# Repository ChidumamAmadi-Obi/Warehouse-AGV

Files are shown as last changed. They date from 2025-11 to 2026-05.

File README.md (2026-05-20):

# Warehouse AGV 
*(3rd Year Capstone Project)*

Automated Guided Vehicle that transports loads along predetermined paths. Features line following, obstacle detection, location tracking, and PS4 controller input via Bluetooth. Built with a Finite State Machine (FSM) architecture with LED/buzzer alerts for user feedback.

### Links
 - [**Demo Video**](https://github.com/user-attachments/assets/4ddb8e79-1c91-4d6d-a385-816ef9b9aa53) <br>
 - [*STL Files*](https://github.com/ChidumamAmadi-Obi/Warehouse-AGV/tree/main/mechanical%20design/STL%20FIles) <br>
 - [*Gerber Files*](https://github.com/ChidumamAmadi-Obi/Warehouse-AGV/tree/main/hardware/gerbers-files) <br>
 - [*Schematic Diagram*](https://github.com/ChidumamAmadi-Obi/Warehouse-AGV/blob/main/hardware/schematic-pdf.pdf) <br>
 - [*Firmware Source Code*](https://github.com/ChidumamAmadi-Obi/Warehouse-AGV/tree/main/firmware) <br>



### Features
- PS4 Bluetooth controller for destination waypoints
- Line following with obstacle avoidance
- Real-time location tracking with waypoint markers on track
- Finite State Machine with robust transitions 
- Visual/audio alerts (LEDs & buzzer)
- 3D printable chassis (STL files included)
- Custom PCB with integrated motor driver, voltage regulation and sensor headers

### Firmware Prerequisites
The chosen controller needs to be paired with the ESP32’s Bluetooth MAC address before use.
Additionally, project also relies on [this](https://github.com/pablomarquez76/PS4_Controller_Host/tree/main) ps4 controller library to handle the Bluetooth communication between the ESP32 and the PS4 controller.

Once this library is installed it is to be inserted into the `./lib` PlatformIO project directory

### Custom PCB


### Schematic Diagram


### State Diagram


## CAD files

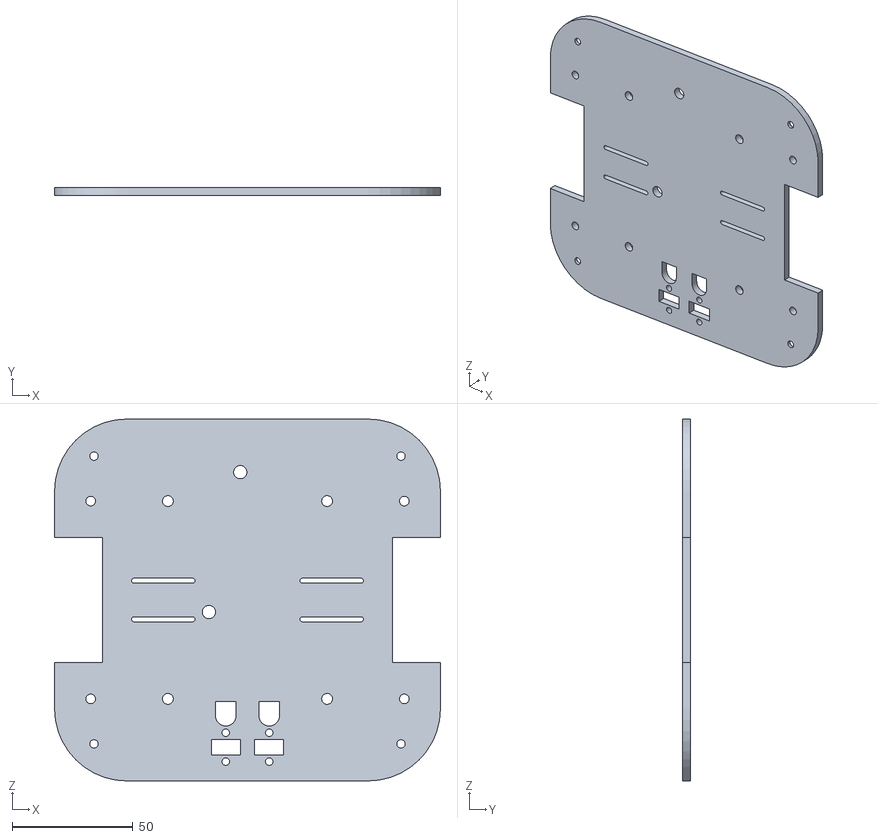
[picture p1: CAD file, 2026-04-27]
mechanical design/STL FIles/Bottom.STL
160.0 x 3.50 x 150.0

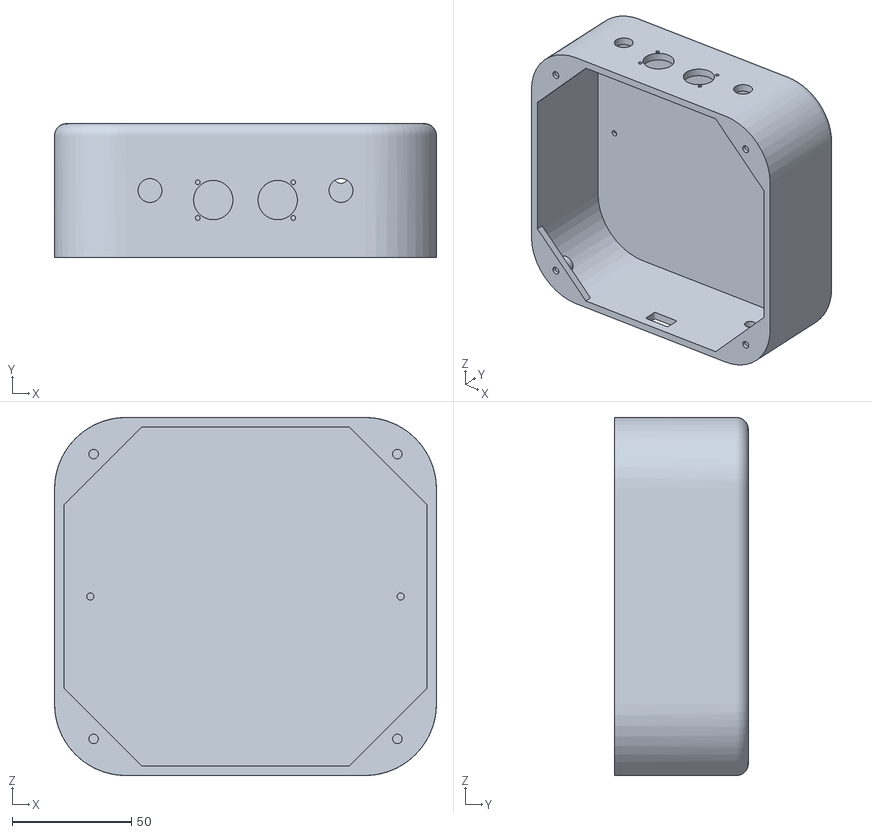
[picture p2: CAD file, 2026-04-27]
mechanical design/STL FIles/Body.STL
160.0 x 56.0 x 150.0

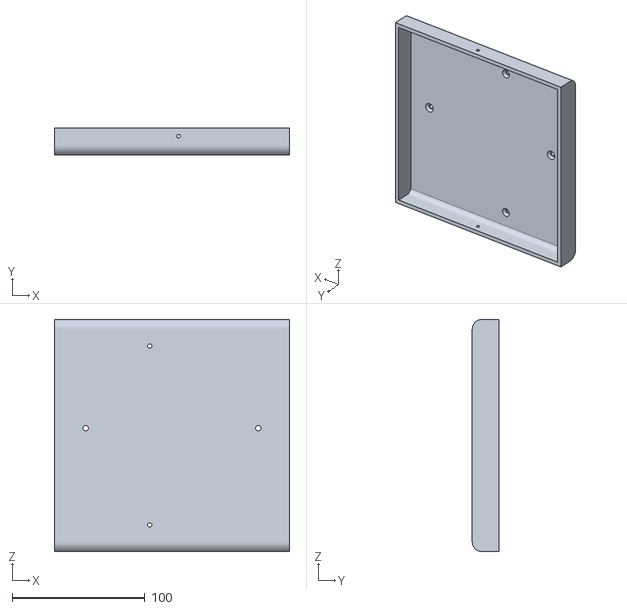
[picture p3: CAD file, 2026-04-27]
mechanical design/STL FIles/Top.STL
177.0 x 20.0 x 175.0

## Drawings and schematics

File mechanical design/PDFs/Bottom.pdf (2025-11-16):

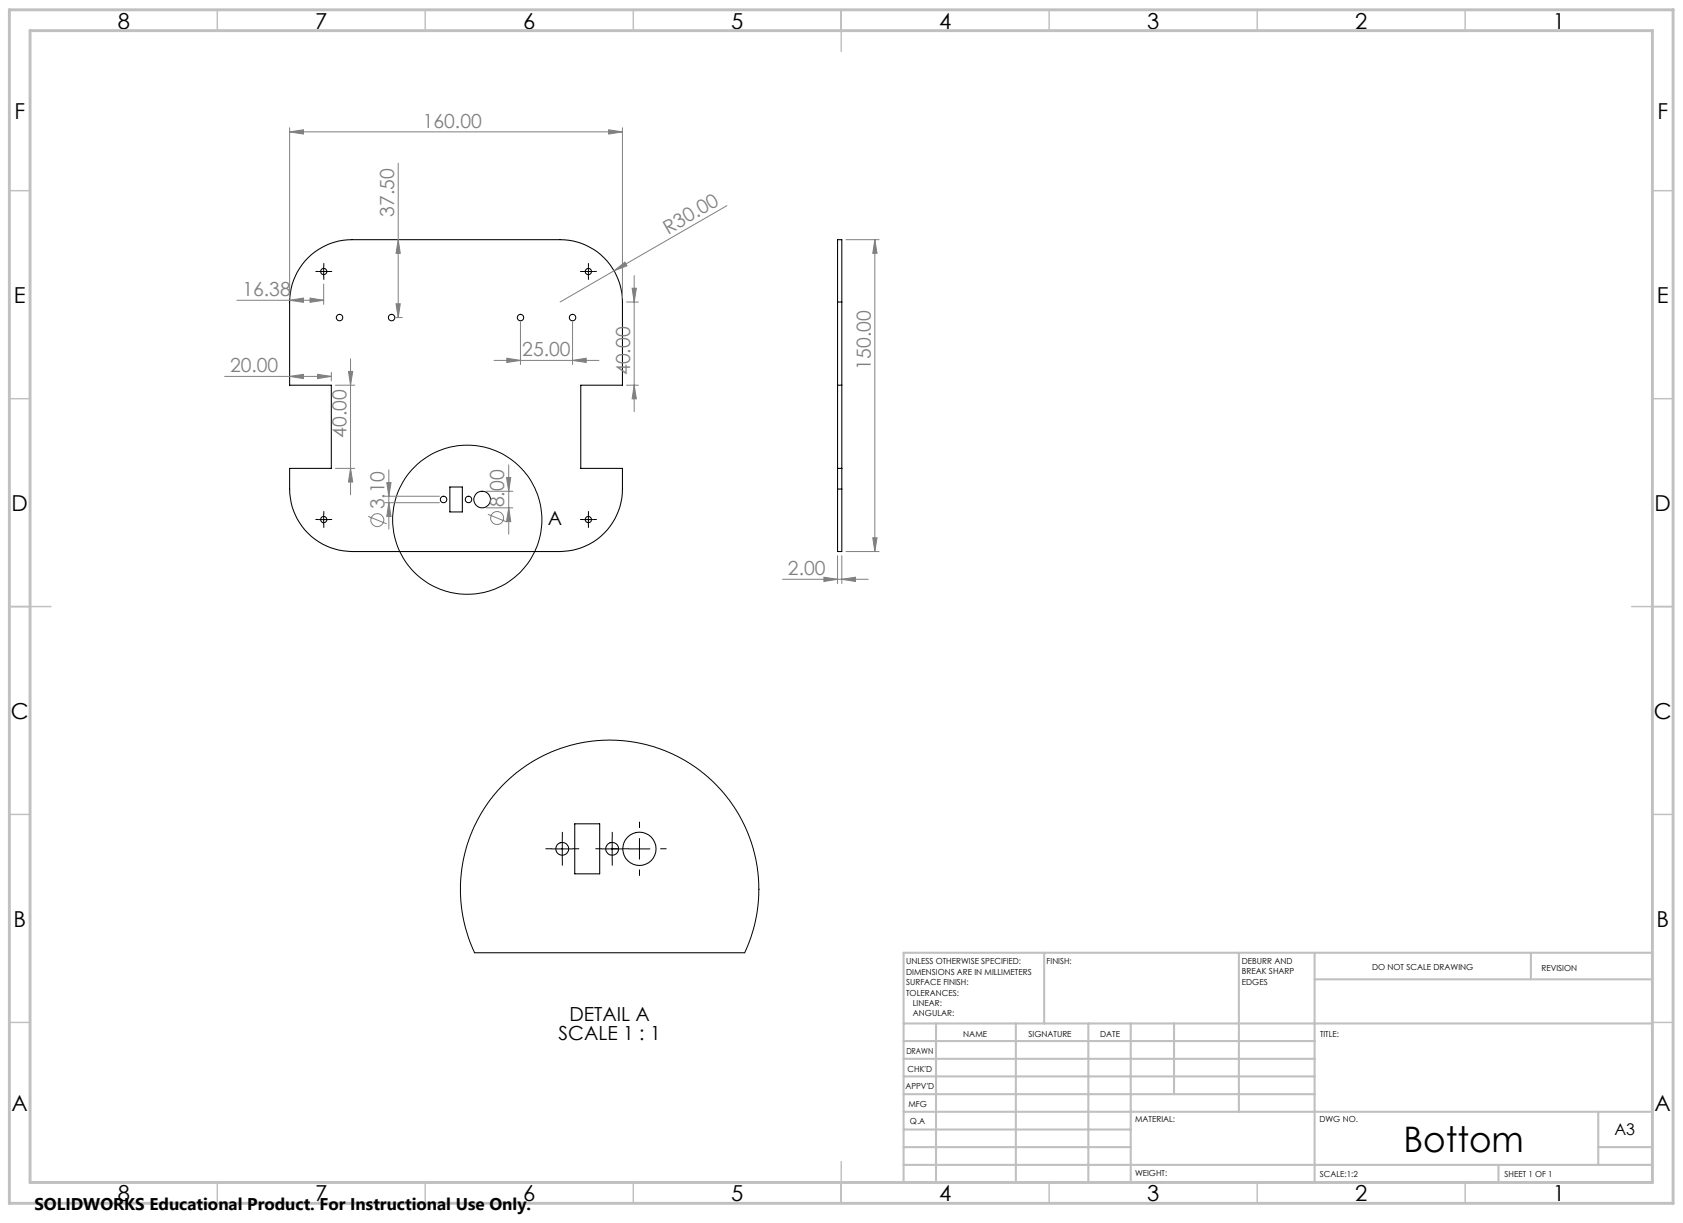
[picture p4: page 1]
DETAIL A SCALE 1 : 1; FINISH:; DEBURR AND; BREAK SHARP; DO NOT SCALE DRAWING; REVISION; SCALE:1:2; SHEET 1 OF 1

UNLESS OTHERWISE SPECIFIED:
DIMENSIONS ARE IN MILLIMETERS
SURFACE FINISH:
TOLERANCES:
LINEAR:
ANGULAR:

NAME | SIGNATURE | DATE | | | | TITLE:

DRAWN
CHK'D
APPV'D
MFG
Q.A | | | | MATERIAL: | DWG NO. Bottom | A3

SOLIDWORKS Educational Product. For Instructional Use Only.

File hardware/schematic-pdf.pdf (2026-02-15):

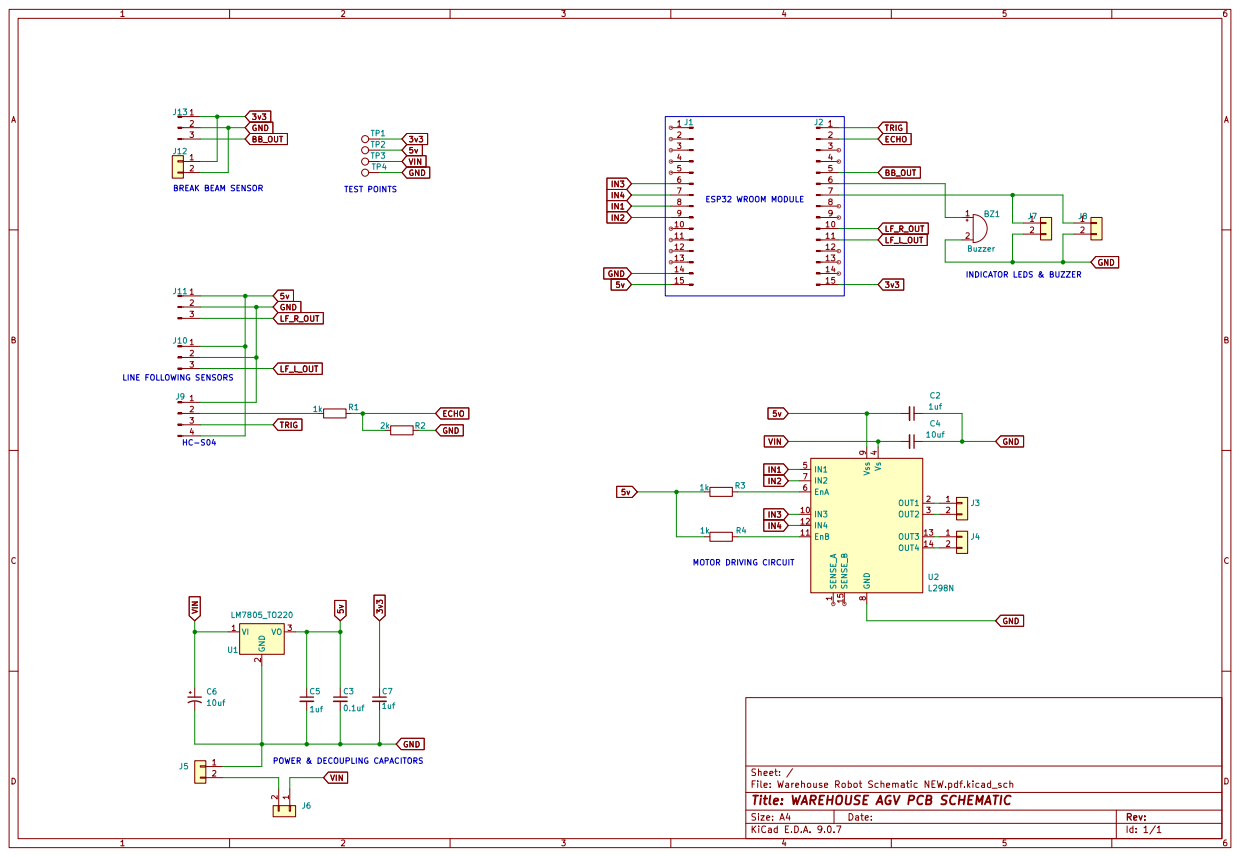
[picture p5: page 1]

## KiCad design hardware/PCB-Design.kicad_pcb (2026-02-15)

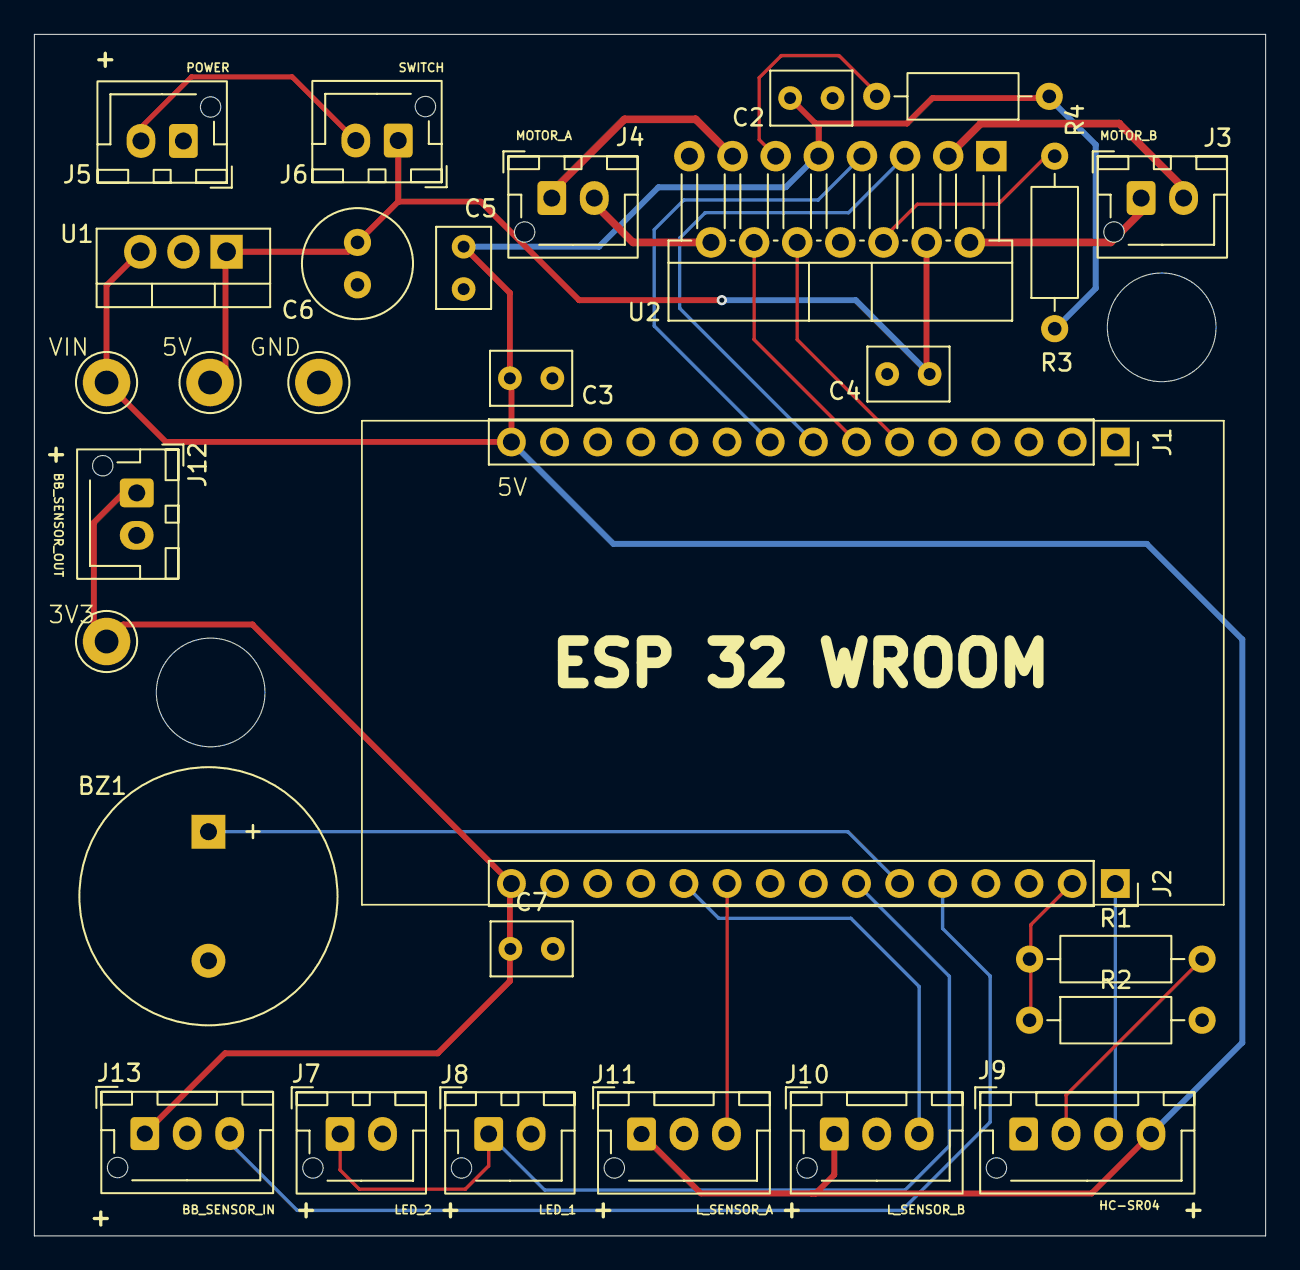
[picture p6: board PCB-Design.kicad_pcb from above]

Board: 2 copper layers, 72.5 x 70.8 mm, 30 parts (0 on the bottom side), 23 nets.

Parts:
BZ1: Buzzer; Buzzer_15x7.5RM7.6
C2, C5, C7: 1uf; C_Rect_L4.6mm_W3.0mm_P2.50mm_MKS02_FKP02
C3: 0.1uf; C_Rect_L4.6mm_W3.0mm_P2.50mm_MKS02_FKP02
C4: 10uf; C_Rect_L4.6mm_W3.0mm_P2.50mm_MKS02_FKP02
C6: 10uf; C_Radial_D6.3mm_H5.0mm_P2.50mm
J1, J2: Conn_01x15_Pin; PinSocket_1x15_P2.54mm_Vertical
J3, J4, J5, J6, J7, J8, J12: Conn_01x02; JST_XH_B2B-XH-AM_1x02_P2.50mm_Vertical
J9: Conn_01x04_Pin; JST_XH_B4B-XH-AM_1x04_P2.50mm_Vertical
J10, J11, J13: Conn_01x03_Pin; JST_XH_B3B-XH-AM_1x03_P2.50mm_Vertical
R1, R3, R4: 1k; R_Axial_DIN0207_L6.3mm_D2.5mm_P10.16mm_Horizontal
R2: 2k; R_Axial_DIN0207_L6.3mm_D2.5mm_P10.16mm_Horizontal
TP1, TP2, TP3, TP4: TestPoint; TestPoint_Loop_D3.50mm_Drill1.4mm_Beaded
U1: LM7805_TO220; TO-220-3_Vertical
U2: L298N; TO-220F-15_P2.54x5.08mm_StaggerOdd_Lead5.08mm_Vertical

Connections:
3v3: C7.1, J2.15, J12.1, J13.1, TP1.1
5v: C2.2, C3.1, C5.1, J1.15, J9.4, J10.1, J11.1, R3.1, R4.1, TP2.1, U1.3 (VO), U2.9 (Vss)
BB_OUT: J2.5, J13.3
ECHO: J2.2, R1.2, R2.1
GND: BZ1.2 (-), C2.1, C3.2, C4.1, C5.2, C6.2, C7.2, J1.14, J5.1, J7.2, J8.2, J9.1, J10.2, J11.2, J12.2, J13.2, R2.2, TP4.1, U1.2 (GND), U2.8 (GND)
IN1: J1.8, U2.5 (IN1)
IN2: J1.9, U2.7 (IN2)
IN3: J1.6, U2.10 (IN3)
IN4: J1.7, U2.12 (IN4)
LF_L_OUT: J2.11, J10.3
LF_R_OUT: J2.10, J11.3
unnamed: BZ1.1 (+), J2.6
unnamed: J2.7, J7.1, J8.1
unnamed: J3.1, U2.2 (OUT1)
unnamed: J3.2, U2.3 (OUT2)
unnamed: J4.1, U2.13 (OUT3)
unnamed: J4.2, U2.14 (OUT4)
unnamed: J5.2, J6.2
unnamed: J9.2, R1.1
unnamed: R3.2, U2.6 (EnA)
unnamed: R4.2, U2.11 (EnB)
TRIG: J2.1, J9.3
VIN: C4.2, C6.1, J6.1, TP3.1, U1.1 (VI), U2.4 (Vs)

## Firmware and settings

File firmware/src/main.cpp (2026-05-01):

/* MAIN PROGRAM
author: Chidumam Amadi-Obi
student number: B00167937

NOTES:
after removing unnessesary code, the robot followed the line almot perfectly, it is going off track at specific points so that is easily fixable

to detect the cross / docking station, the robot times how long it is detecting a cross (both line sensors are low as no light is reflected)
if both sensors are low for a specific amount of time the robot will dock
this is because there are many false positivves of cross detection for split seconds.

the line the robot follows was also made thinner so the robot does not oscillate too much

removed watch dog timer

*/

#include "agv_controller.h"

// ***************************************************************
void initGPIO() { // assigns needed pins as inputs or outputs
  pinMode(TRIG_PIN, OUTPUT);
  pinMode(ECHO_PIN, INPUT);

  pinMode(MOTOR_PIN_A1, OUTPUT);
  pinMode(MOTOR_PIN_A2, OUTPUT);
  pinMode(MOTOR_PIN_B1, OUTPUT);
  pinMode(MOTOR_PIN_B2, OUTPUT);

  pinMode(LED_PIN, OUTPUT);
  pinMode(BUZZER_PIN, OUTPUT);
  pinMode(BB_PIN, INPUT);
  pinMode(L_IR_PIN,INPUT);
  pinMode(R_IR_PIN,INPUT);

  analogWrite(MOTOR_PIN_A1, 0);// starts all outputs as low
  analogWrite(MOTOR_PIN_A2, 0);
  analogWrite(MOTOR_PIN_B1, 0);
  analogWrite(MOTOR_PIN_B2, 0);

  digitalWrite(LED_PIN, LOW); 
  digitalWrite(BUZZER_PIN, LOW);
  digitalWrite(TRIG_PIN, LOW);
  L298Driver(STOP,OFF); 
}

void calliIRSensors(){ // callibrate ir line following sensors and test line following of robot
  lineFollowingAlgo();
  line.cross ?  digitalWrite(LED_PIN,HIGH) :  digitalWrite(LED_PIN,LOW); // leds turn on when robot crosses docking station
}

// ***************************************************************

void setup() {
  Serial.begin(115200);
  initGPIO();
  PS4.begin(); // initializes ps4 controller with esp32
  if (!PS4.isConnected()) Serial.println("ERROR CONNECTING PS4 CONTROLLER, CONTINUING WITHOUT BLUETOOTH...");
  melodyManager(ERROR_MELODY);
  Serial.println("AGV INITALIZED!");

}

void loop() {
  AGVStateMachine(); // state machine is called forever

  delay(10);
}



/* refs
print to terminal in color https://gist.github.com/RabaDabaDoba/145049536f815903c79944599c6f952a
*/

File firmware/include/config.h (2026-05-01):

/* CONFIG
 this is where macros, constants, structs and enums used by all 
 source/header files are defined
 needed librarys are also included here
 macros can be edited here to changes the behaviour of
 the program
*/

#pragma once

#include <Arduino.h> // for arduino framework functions
#include <PS4Controller.h> // for ps4 bluetooth control

// define pin numbers
#define TRIG_PIN    23
#define ECHO_PIN    22
#define BUZZER_PIN  19
#define LED_PIN     18
#define BB_PIN      21
#define L_IR_PIN    16
#define R_IR_PIN    4
#define MOTOR_PIN_A1 25
#define MOTOR_PIN_A2 26
#define MOTOR_PIN_B1 32
#define MOTOR_PIN_B2 33

// config macros
#define SCAN_INTERVAL 200 // (ms) interval at which the ultrasonic distance sensor scans for objects
#define CROSS_TIMER 225 // (ms) 
#define CORSE_CORRECTION_INTERVAL 80 // (ms)
#define LOCATION_TRACK_INTERVAL 1000 // (ms)
#define OBSTACLE_DETECTION_THRESHOLD 10 // 10cm
#define IS_MUTED 0 // set as 1 if you dont want the buzzer to play music at all

#define REST 50 // ms, music speed

// dont touch these macros
#define SPEED_OF_SOUND 0.034 // used to calculate distance

typedef enum { // defines direction codes for motor driver
    RIGHT,
    LEFT,
    FORWARD,
    BACKWARD,
    STOP
} Dir;

typedef enum { // valid ps4 controller inputs that can be processed by the agv
    STATION_NONE=-1,
    STATION_HOME,
    STATION_ONE,
    STATION_TWO,
    STATION_THREE,
    
    EMERGENCY_STOP,
} PS4Inputs;

typedef enum { // for agv states
    STATUS_IDLE,                    // waiting for a package, and a destination
    STATUS_TRAVELLING,              // traveling to destination
    STATUS_OBSTACLE_OBSTRUCTION,    // pausing until obstacle is removed
    STATUS_UNLOADING,               // when destination is reached...
    STATUS_ERROR 
} AGVState;

typedef enum { // defines melody codes for melody manager
    STARTUP_MELODY,
    OBJECT_DETECTED_MELODY,
    DESTINATION_REACHED_MELODY,
    ERROR_MELODY,
    PACKAGE_RECEIVED_MELODY,
    SLOW_BEEP,
    FAST_BEEP,
} Melodies;

typedef enum { // set speed modes for robot
    OFF = 0,
    CRUISING_SPEED = 125,
    MAX_SPEED = 255
} SpeedModes;

typedef enum { // define error states here for future error checking
    NO_ERROR,
    PACKAGE_ERROR
} Errors;


// using a struct encapsulates similar data making code more readable
typedef struct { // for agv status flags and other variables
    AGVState currentAGVState = STATUS_IDLE;  // keeps track of agv state
    Errors error = NO_ERROR;

    bool isDestinationReached = false;
    bool isCarryingLoad = false;
    bool isPathObstructed = false;  
    bool hasBeenAlerted = false;
    bool hasDestination = false;
    unsigned long lastLineCorrection = 0.0; 
    uint8_t agvDestination = -1; // -1 means no chosen destination 
    uint8_t agvLocation = 0; // keeps track of which docking spot the robot is (0-3)
} AGVStatusFlags;

typedef struct { // flags for ir line followin sensors
    bool statusR = false; // on line
    bool statusL = false; // on line
    bool cross = false; // detects if bot is at a cross
} LineStatusFlags;

typedef struct {
    unsigned long crossTimer=0;
    unsigned long lastDestinationIncriment;
    unsigned long lastDistanceSensorScan;
    unsigned long prevLEDMillis; 
} Timing;

Timing timing; // initialize timing struct in config so all files can access it

// refs & explanations
// https://www.w3schools.com/c/c_enums.php 
// https://www.geeksforgeeks.org/c/structures-c/
// https://riptutorial.com/c/example/7662/header-include-guards
// https://iotassistant.io/esp32/enable-hardware-watchdog-timer-esp32-arduino-ide/ watchdog timer 

/*

enums were used here to give names to constant values, it makes
the program easier to read and maintain 
by default, the first member of an enum is equal to 0
the second is equal to 1 and so on

structs were used here to group related variables of different data types
into a single unit, making it easier to manage and organize complex data.
for example we have a struct for the AGV, this struct is used to store various bits
of information about the AGV like its location, state, load and sensor inputs

header gaurds were used here to make sure when header files are includes in multiple
places, like config.h, there are no duplicate delcarations

*/

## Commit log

2025-11-04 Added voltage dividers to sensor outputs
    Voltage dividers were used to convert the output of sensors of a 5V logic level to a 3V3 logic level and safely input into the ESP32
2025-11-12 mechanical design of chassis with solidworks
    [Body.SLDDRW, Body.SLDPRT, Bottom.SLDDRW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]
2025-11-23 added AGV control logic implimentation
    added control logic for the AGV with state based programming and a switch case structure. more comments, explanations and references
2025-11-25 flowchart update
2025-11-26 updated flowchart
2026-01-29 remade/updated schematic in kicad
    [Warehouse Robot Schematic NEW.kicad_sch]
2026-01-29 Update and rename Warehouse Robot Schematic NEW.kicad_sch to Warehouse Robot Schematic.kicad_sch
    [Warehouse Robot Schematic.kicad_sch]
2026-02-02 updated schematic with test points
2026-02-06 integrated ps4 controller into code, fixed bugs
    [config.h, main.cpp]
2026-02-06 merged motor_driver.h and sensor_drivers.h
2026-02-06 Update and rename sensor_drivers.h to drivers.h
2026-02-07 PCB design
    [Warehouse Robot Schematic NEW.pdf.kicad_pcb]
2026-02-07 Add new PCB design for Warehouse Robot
    [Warehouse Robot PCB Design.kicad_pcb]
2026-02-15 updated schematic and pcb design
    [Warehouse Robot PCD Design.kicad_pcb]
2026-02-18 Add new PCB preview image to README
2026-02-21 Update and rename Warehouse Robot PCD Design.kicad_pcb to Warehouse Robot PCB Design.kicad_pcb
    [Warehouse Robot PCB Design.kicad_pcb]
2026-04-21 Basic AGV functionality working
    proper package detection
    proper ir line detection
    complete line following algorithm
    complete and fixed state machine
    made function for ir line sensor calibration and AGV line following test
    [config.h, main.cpp]
2026-04-27 upload STL files
    [Body.STL, Bottom.STL, Top.STL]
2026-05-01 final firmware changes
    buzzer sounds were made to be less annoying and constant,
    configuration macros fine tuned
    [config.h, main.cpp]
2026-05-19 Rename Warehouse Robot PCB Design.kicad_pcb to PCB-Design.kicad_pcb
    [PCB-Design.kicad_pcb]
2026-05-19 Add Warehouse Robot schematic file
    [schematic.kicad_sch]
2026-05-19 Rename Warehouse Robot Schematic.pdf to schematic-pdf.pdf
2026-05-20 upload gerber files
    [Warehouse Robot Schematic NEW.pdf-B_Cu.gbl, Warehouse Robot Schematic NEW.pdf-B_Mask.gbs, Warehouse Robot Schematic NEW.pdf-B_Paste.gbp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]
2026-05-20 Update README with additional resources and prerequisites
    Added links to demo video, STL files, Gerber files, schematic diagram, and firmware source code. Included firmware prerequisites for PS4 controller integration.
